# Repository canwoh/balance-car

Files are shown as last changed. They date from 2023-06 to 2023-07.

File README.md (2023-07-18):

# balance-car
## 错误报刊🚫

### 1. PCB设计

#### 滑动开关
开关失效。原理图绘画的时候，把滑动开关其中两个脚都接到了VBAT上，铺铜的时候两脚都接入VBAT，导致开关即使左拨还是右拨中间引脚都会上电。

解决方案：给电源盒焊个开关，将电源盒引出的线接到开关上，再接入PCB中。

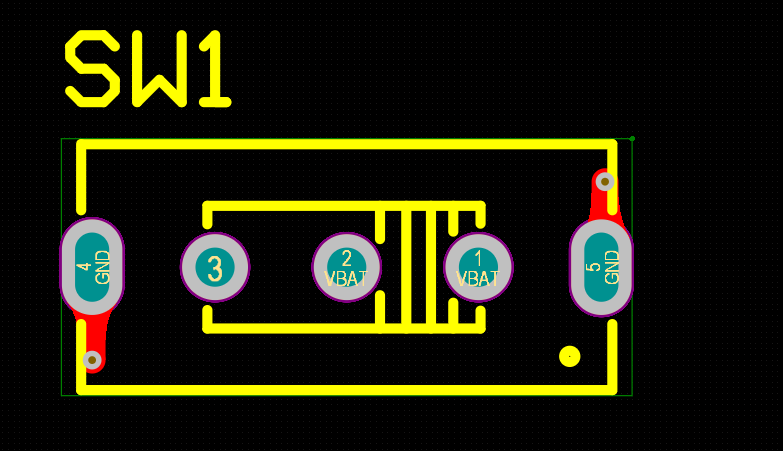
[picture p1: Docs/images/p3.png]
switch


#### OLED模块：
GND与VCC刚好相反，导入PCB封装与实际不符。

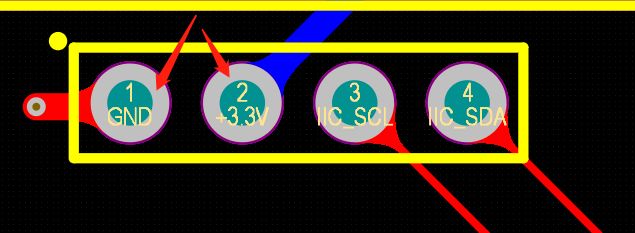
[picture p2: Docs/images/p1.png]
PCB中OLED


#### 电机模块：
注意同一轮子放在左右两侧，DRV8833 相同OUX输出出现两轮转向不一致的情况。

解决方案：右轮BO1与BO2在焊接时，反焊，左轮AO1->AO1 AO2->AO2  右轮BO1->BO2 BO2->BO1

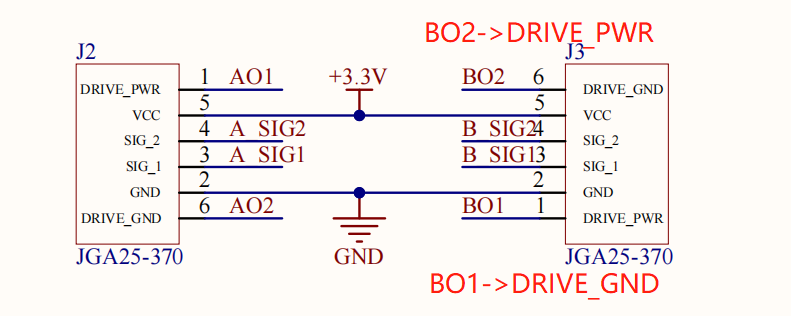
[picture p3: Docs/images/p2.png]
Motor


### 2.CubeMX初始化代码
#### Motors初始化
给电机少配置了两个TIM-PWM输出。PCB设计时给电机配置了两个GPIO，与两个TIM-PWM，实际需要4个PWM输出。

解决方案：后续软件上配置两个PWM Channel，利用中断控制GPIO电平，普通GPIO模拟PWM输出。

### 3.软件编写
#### 软件模拟IIC
* 时序控制错误，移植代码后没有调节时序延迟。查看SSD1306硬件手册时序在400KB/s模式下保底需要2.5us延迟。

* 软件模拟IIC，注意FreeRTOS任务切换时引起的时序问题。

#### FreeRTOS Task Stack Overflow问题
* 任务栈分配不足时，引发一些奇怪的现象。

#### 

## 项目改进🧐
* 项目采用MCU为STM32F103C8T6，Flash空间太小了，只有64KB。采用HAL+FreeRTOS+C/C++混合编写的组合还是太吃力了。编写代码大小受到较大限制。可尝试更换性能更好的MCU。

* 电源模块可以单独拎出来设计，贴片更加方便，压缩水平空间，降低体积。

* 有线器件，可以选择XH接插件方式进行连接。

* 额外设计一个USB串口兼下载模块，版上集成CMSIS-DAP模块(参考项目：vllink_lite)

* 项目中为了学习DMA，蓝牙模块采用UART+DMA模式，推荐采用中断UART接收形式。DMA接收定长输入的效果会更好一些，由于我所使用的上位机发送的信息是不定长且较短，不太好接收。当然DMA接收不定长输入也行，配合中断即可。

## 硬件参考

* 显示屏:OLED 0.96
* 惯性测量单元:MPU6050
* 电机驱动芯片:DRV8833
* 超声波:HC-SR04
* 蓝牙:HC-05
* 电机：淘宝随便买的

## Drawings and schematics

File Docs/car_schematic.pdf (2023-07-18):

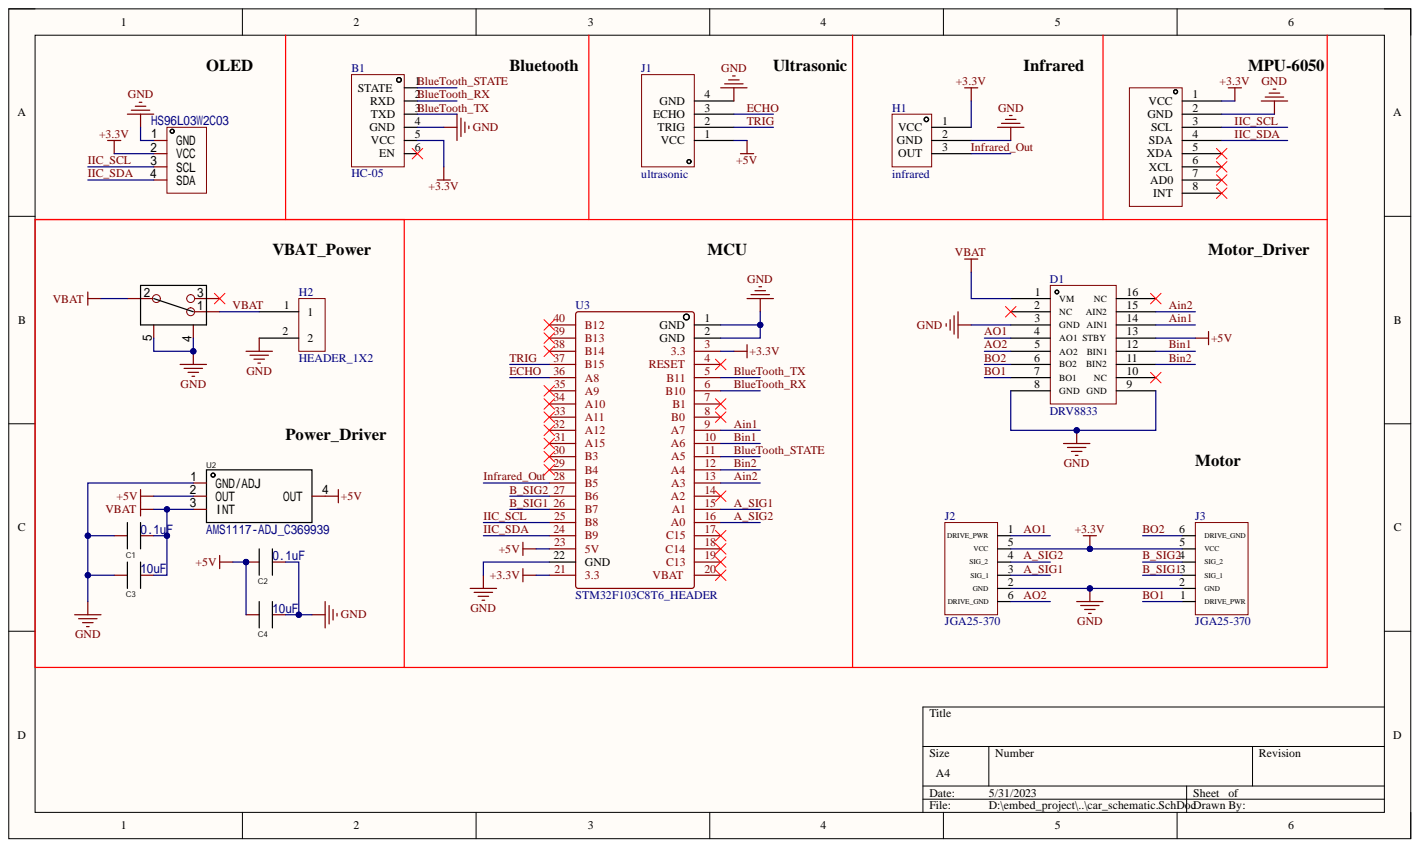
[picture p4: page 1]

Size A4 | Number | Revision

Date: 5/31/2023 | Sheet of
File: D:\embed_project\..\car_schematic.SchDocDrawn By:

Comment | Description | Designator | Footprint | LibRef | Quantity
HC-05 | 蓝牙模块 VCC接3.3 | B1 | HC-05_HEADER | HC-05 | 1
0.1uF | | C1, C2 | C0603 | C0603 | 2
10uF | | C3, C4 | C0603 | C0603 | 2
DRV8833 | 电机驱动 | D1 | DRV8833_HEADER | DRV8833 | 1
infrared | 红外循迹模块 | H1 | RISYM-001_HEADER | RISYM-001 | 1
HEADER_1X2 | | H2 | HEADER_1X2 | HEADER_1X2 | 1
ultrasonic | 超声波模块 Pin Header | J1 | HC-SR04_HEADER | HC-SR04 | 1
JGA25-370 | JGA25-370 直流减速 电机 | J2, J3 | JGA25-370_HEADER | JGA25-370 | 2
SS-12F44-G5_C136718 | 滑动开关G5 | SW1 | SW-TH_SS-12F44-GX | SS-12F44-G5_C136718 | 1
MPU-6050 | Pin Header | U1 | MPU-6050_HEADER | MPU-6050 | 1
AMS1117-ADJ_C369939 | 电源稳压芯片 | U2 | SOT-223_L6.5-W3.5-P2.30-LS7.0-BR | AMS1117-ADJ_C369939 | 1
STM32F103C8T6_HE ADER | Pin Header | U3 | STM32F103C8T6_HE ADER | STM32F103C8T6_HE ADER | 1
HS96L03W2C03 | I2C OLED 0.96 | U4 | OLED-TH_L27.8-W27.2-P2.54_C9900033791 | HS96L03W2C03 | 1

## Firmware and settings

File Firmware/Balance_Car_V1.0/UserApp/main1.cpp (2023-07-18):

#include "common_inc.h"
#include "mpu6050.h"

#define OLED_ADDRESS 0x78
//------------------------c header file scope----------------------------------------
#ifdef __cplusplus
extern "C"
{
#endif
#include "inv_mpu.h"
#include "OLED_Driver.h"
#include <cstring>
#include "bluetooth.h"
#include"control.h"
#ifdef __cplusplus
}
#endif
//----------------------------------------------------------------

// SSD1306 screen(OLED_ADDRESS);
IMU_MPU6050 imu_6050;
//----------------------FreeRtos-----------
extern osMessageQueueId_t uart_rx_dma_queue_id;
extern osThreadId_t defaultTaskHandle;
extern osThreadId_t IMUHandle;
extern osThreadId_t ultrasonicHandle;
//----------------------debug code------
extern char debug_data[8];
uint8_t complete_record;

uint8_t motor_run = 0;
// extern osThreadId_t defaultTaskHandle;
// extern osThreadId_t IMUHandle;
// extern osThreadId_t ultrasonicHandle;
// extern uint32_t time_record[4];
//-----------------User data------------
extern float dist;
extern uint8_t uart_rx_dma_buffer[BUFFER_SIZE];

int balance_pwm,velocity_pwm;
int encoder_left, encoder_right;
int motor1_pwm,motor2_pwm;
//---------------firmware code----------
extern DMA_HandleTypeDef hdma_usart3_rx;
extern UART_HandleTypeDef huart3;
extern TIM_HandleTypeDef htim3;
/*------------------------------------------C++ scope------------------------------------*/
void Motion_Controller_Thread(void *args)
{
    Motor_Init();
    // HAL_GPIO_WritePin(GPIOA,GPIO_PIN_3,GPIO_PIN_RESET);
    // HAL_GPIO_WritePin(GPIOA,GPIO_PIN_4,GPIO_PIN_RESET);
    // __HAL_TIM_SET_COMPARE(&htim3,TIM_CHANNEL_1,MOTOR_DEAD_ZONE);
    // __HAL_TIM_SET_COMPARE(&htim3,TIM_CHANNEL_2,MOTOR_DEAD_ZONE);
    for(;;)
    {
        //读编码器
        encoder_left = Read_Encoder(1);
        encoder_right = -Read_Encoder(2); 
        //直立环
        balance_pwm = Vertical_Ring_PD(imu_6050.imu_data_t.pitch,
                                       imu_6050.imu_data_t.gyro_y);
        //速度环
        velocity_pwm = Velocity_Ring_PI(encoder_left, encoder_right,imu_6050.imu_data_t.pitch);
        motor1_pwm = balance_pwm+velocity_pwm;
        motor2_pwm = balance_pwm+velocity_pwm;
        Motor_Limit(&motor1_pwm,&motor2_pwm);
        if(Turn_OFF(imu_6050.imu_data_t.pitch)){
            __HAL_TIM_SET_COMPARE(&htim3,TIM_CHANNEL_1,0);
            __HAL_TIM_SET_COMPARE(&htim3,TIM_CHANNEL_2,0);
            __HAL_TIM_SET_COMPARE(&htim3,TIM_CHANNEL_3,0);  
            __HAL_TIM_SET_COMPARE(&htim3,TIM_CHANNEL_4,0);  
        }else {
            Set_PWM(motor1_pwm,motor2_pwm);
        }
        osDelay(10);
    }
}

void UART_Recv_DMA_Thread(void *args)
{
    
    HAL_UART_Receive_DMA(&huart3, uart_rx_dma_buffer, BUFFER_SIZE);
    complete_record = 2;
    void *d;
    for (;;)
    {
        osMessageQueueGet(uart_rx_dma_queue_id, &d, NULL, osWaitForever);
        complete_record = 1;
        usart_tx_check();
        (void)d;
    }
}
// ultrasonic measuring distance  25Hz task
void Measure_Distance(void *args)
{
    HAL_GPIO_WritePin(Echo_GPIO_Port, Echo_Pin, GPIO_PIN_RESET);
    for (;;)
    {
        HAL_GPIO_WritePin(Trig_GPIO_Port, Trig_Pin, GPIO_PIN_SET);
        mDelay_us(15);
        HAL_GPIO_WritePin(Trig_GPIO_Port, Trig_Pin, GPIO_PIN_RESET);
        osDelay(40);
    }
}

// imu task handle function 200Hz task
void IMU_Get_Data(void *args)
{
    vTaskSuspendAll();
    while (mpu_dmp_init())
    {
    }

    OLED_Init();
    xTaskResumeAll();
    for (;;)
    {
        vTaskSuspendAll();
        mpu_dmp_get_data(&imu_6050.imu_data_t);

        xTaskResumeAll();
        osDelay(5);
    }
}
// initialize and show data 5Hz task
// void Main(void *args)
// {
//     OLED_Init();
//     Motor_Init();
//     HAL_GPIO_WritePin(GPIOA,GPIO_PIN_3,GPIO_PIN_RESET);
//     HAL_GPIO_WritePin(GPIOA,GPIO_PIN_4,GPIO_PIN_RESET);
//     __HAL_TIM_SET_COMPARE(&htim3,TIM_CHANNEL_1,MOTOR_DEAD_ZONE);
//     __HAL_TIM_SET_COMPARE(&htim3,TIM_CHANNEL_2,MOTOR_DEAD_ZONE);
//     //char *msg = (char *)pvPortMalloc(16);
//     for (;;)
//     {
//         vTaskSuspendAll();
//         // OLED_ShowString(1,1,"mem:")
//         // memset(msg, 0, 16);
//         // sprintf(msg, "pitch:%.5f", imu_6050.imu_data_t.pitch);
//         // OLED_ShowString(1, 1, msg);
//         // // printf("%s\r\n",msg);
//         // memset(msg, 0, 16);
//         // sprintf(msg, "roll:%.5f", imu_6050.imu_data_t.roll);
//         // OLED_ShowString(2, 1, msg);
//         // // printf("%s\r\n",msg);
//         // memset(msg, 0, 16);
//         // sprintf(msg, "yaw:%.5f", imu_6050.imu_data_t.yaw);
//         // OLED_ShowString(3,1,msg);


//         OLED_ShowNum(4,1,motor_run,4);
      
//         xTaskResumeAll();
//         osDelay(200);
//     }
//     // vPortFree(msg);
// }

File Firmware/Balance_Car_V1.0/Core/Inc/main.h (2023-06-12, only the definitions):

#define AIN2_Pin GPIO_PIN_3
#define AIN2_GPIO_Port GPIOA
#define BIN2_Pin GPIO_PIN_4
#define BIN2_GPIO_Port GPIOA
#define Bluetooth_State_Pin GPIO_PIN_5
#define Bluetooth_State_GPIO_Port GPIOA
#define Trig_Pin GPIO_PIN_15
#define Trig_GPIO_Port GPIOB
#define Echo_Pin GPIO_PIN_8
#define Echo_GPIO_Port GPIOA
#define Echo_EXTI_IRQn EXTI9_5_IRQn
#define infrared_Pin GPIO_PIN_5
#define infrared_GPIO_Port GPIOB
#define I2C_SCL_Pin GPIO_PIN_8
#define I2C_SCL_GPIO_Port GPIOB
#define I2C_SDA_Pin GPIO_PIN_9
#define I2C_SDA_GPIO_Port GPIOB

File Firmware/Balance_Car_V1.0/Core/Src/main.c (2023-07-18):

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
/* Includes ------------------------------------------------------------------*/
#include "main.h"
#include "cmsis_os.h"
#include "dma.h"
#include "tim.h"
#include "usart.h"
#include "gpio.h"

/* USER CODE BEGIN Includes */
#include"OLED_Driver.h"
extern uint8_t complete_record;
extern osMessageQueueId_t uart_rx_dma_queue_id;
extern uint32_t time_record[4];
extern float dist;

/* USER CODE END Includes */


void SystemClock_Config(void);
void MX_FREERTOS_Init(void);
/**
  * @brief  The application entry point.
  * @retval int
  */
int main(void)
{
  /* MCU Configuration--------------------------------------------------------*/

  /* Reset of all peripherals, Initializes the Flash interface and the Systick. */
  HAL_Init();

  /* Configure the system clock */
  SystemClock_Config();

  /* Initialize all configured peripherals */
  MX_GPIO_Init();
  MX_DMA_Init();
  MX_USART3_UART_Init();
  MX_TIM2_Init();
  MX_TIM3_Init();
  MX_TIM4_Init();
  /* Init scheduler */
  osKernelInitialize();  /* Call init function for freertos objects (in freertos.c) */
  MX_FREERTOS_Init();

  /* Start scheduler */
  osKernelStart();
  /* We should never get here as control is now taken by the scheduler */
  /* Infinite loop */
  /* USER CODE BEGIN WHILE */
  while (1)
  {
    /* USER CODE END WHILE */
    
    /* USER CODE BEGIN 3 */
  }
  /* USER CODE END 3 */
}

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
/* USER CODE BEGIN 4 */

/**
  * @brief  PWM Pulse finished callback in non-blocking mode
  * @param  htim TIM handle
  * @retval None
  */
void HAL_TIM_PWM_PulseFinishedCallback(TIM_HandleTypeDef *htim)
{
    // if(htim->Instance == TIM3)
    // {
    //   if(htim->Channel == HAL_TIM_ACTIVE_CHANNEL_3)
    //   {
    //      HAL_GPIO_WritePin(GPIOA,GPIO_PIN_3,RESET);
    //   }
    //   if(htim->Channel == HAL_TIM_ACTIVE_CHANNEL_4)
    //   {
    //     HAL_GPIO_WritePin(GPIOA,GPIO_PIN_4,RESET);
    //   }
    // }
    if(htim->Channel == HAL_TIM_ACTIVE_CHANNEL_3)
    {
        GPIOA->BRR = GPIO_PIN_3;
    } else if(htim->Channel == HAL_TIM_ACTIVE_CHANNEL_4)
    {
        GPIOA->BRR = GPIO_PIN_4;
    }
}



/*
  *@brief UART Callback function
*/
void HAL_UART_RxCpltCallback(UART_HandleTypeDef *huart)
{
  if(USART3 == huart->Instance){
      void *d = (void*)1;
      __HAL_UART_CLEAR_IDLEFLAG(huart);
      osMessageQueuePut(uart_rx_dma_queue_id,&d,0,0);
  }
  //osMessageQueuePut(uart_rx_dma_queue_id,&d,0,0); 
}

/*
  * @brief  Echo Callback
  * @param  GPIO_Pin ：Echo_Pin
  * @retval 无
*/
void HAL_GPIO_EXTI_Callback(uint16_t GPIO_Pin)
{
  __HAL_GPIO_EXTI_CLEAR_IT(GPIO_Pin);
  if(GPIO_Pin == Echo_Pin)
  {
    //pull up trigger
    if(HAL_GPIO_ReadPin(Echo_GPIO_Port,Echo_Pin)==GPIO_PIN_SET)
    {
        time_record[1] = get_sysTick_ms();
        time_record[3] = get_sysTick_us_part();

    }
    //pull down trigger
    else if(HAL_GPIO_ReadPin(Echo_GPIO_Port,Echo_Pin)==GPIO_PIN_RESET)
    {
      //us 
        uint32_t total_time;
        time_record[0] = get_sysTick_ms();
        time_record[2] = get_sysTick_us_part();
        total_time = (time_record[0] - time_record[1])*1000 + time_record[3] - time_record[2]; 
        dist = (float)total_time * 0.17;
    }
  }
}

/* USER CODE END 4 */

/**
  * @brief  Period elapsed callback in non blocking mode
  * @note   This function is called  when TIM1 interrupt took place, inside
  * HAL_TIM_IRQHandler(). It makes a direct call to HAL_IncTick() to increment
  * a global variable "uwTick" used as application time base.
  * @param  htim : TIM handle
  * @retval None
  */
void HAL_TIM_PeriodElapsedCallback(TIM_HandleTypeDef *htim)
{
  /* USER CODE BEGIN Callback 0 */
   if(TIM3->CCR3 != 0)
        GPIOA->BSRR = GPIO_PIN_3;
    if(TIM3->CCR4 != 0)
        GPIOA->BSRR = GPIO_PIN_4;
  /* USER CODE END Callback 0 */
  if (htim->Instance == TIM1) {
    HAL_IncTick();
  }
  /* USER CODE BEGIN Callback 1 */
  // if (htim->Instance == TIM3)
  // {
  //    if((__HAL_TIM_GET_COMPARE(htim,TIM_CHANNEL_3))!=0)
  //     {
  //        HAL_GPIO_WritePin(GPIOA,GPIO_PIN_3,SET);
  //     }
  //     if((__HAL_TIM_GET_COMPARE(htim,TIM_CHANNEL_4))!=0)
  //     {
  //       HAL_GPIO_WritePin(GPIOA,GPIO_PIN_4,SET);
  //     }
  // }
  /* USER CODE END Callback 1 */
}

/**
  * @brief  This function is executed in case of error occurrence.
  * @retval None
  */
void Error_Handler(void)
{
  /* USER CODE BEGIN Error_Handler_Debug */
  /* User can add his own implementation to report the HAL error return state */
  __disable_irq();
  while (1)
  {
  }
  /* USER CODE END Error_Handler_Debug */
}

#ifdef  USE_FULL_ASSERT
/**
  * @brief  Reports the name of the source file and the source line number
  *         where the assert_param error has occurred.
  * @param  file: pointer to the source file name
  * @param  line: assert_param error line source number
  * @retval None
  */
void assert_failed(uint8_t *file, uint32_t line)
{
  /* USER CODE BEGIN 6 */
  /* User can add his own implementation to report the file name and line number,
     ex: printf("Wrong parameters value: file %s on line %d\r\n", file, line) */
  /* USER CODE END 6 */
}
#endif /* USE_FULL_ASSERT */

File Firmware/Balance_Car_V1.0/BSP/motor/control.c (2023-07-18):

#include "control.h"



extern TIM_HandleTypeDef htim2;
extern TIM_HandleTypeDef htim3;
extern TIM_HandleTypeDef htim4;


Motor_PID_ARGS PID_ARGS = {
    .Balance_Kp = -240, //raw value:400 Processed value : -240
    .Balance_Ki = 0,//UNUSED
    .Balance_Kd = -0.68,  //raw value:1.1 Processed value : -0.67
    .Velocity_Kp = -135,
    .Velocity_Ki = -0.67,
    .Velocity_Kd = 0,//UNUSED
    .Turn_Kp = 0,//UNUSED
    .Turn_Ki = 0,//UNUSED
    .Turn_Kd = 0,//UNUSED
};

// 读取编码器值
//@param Motorx(1 or 2) : 1)：编码器1 TIM2  2)：编码器2 TIM4
int Read_Encoder(uint8_t Motorx)
{
    int Encoder_Value;
    switch (Motorx)
    {
    case 1:
        Encoder_Value = (short)TIM2->CNT;
        TIM2->CNT = 0;
        break;
    case 2:
        Encoder_Value = (short)TIM4->CNT;
        TIM4->CNT = 0;
        break;
    default:
        Encoder_Value = 0;
    }
    return Encoder_Value;
}

/***************************************
 *@name：直立PD控制
 *@param：角度、机械平衡角度（机械中值）、角速度
 *@return：直立控制PWM
 *
 */
int Vertical_Ring_PD(float pitch, float Gypo)
{
    float Bias;  // 角度误差
    int balance; // 直立环计算出来的电机控制pwm
    Bias = pitch - MECHANICAL_MEDIAN_ANGLE;
    balance = PID_ARGS.Balance_Kp * Bias + PID_ARGS.Balance_Kd * Gypo;
    return balance;
}


int Velocity_Ring_PI(int Encoder_Left, int Encoder_Right,float pitch)
{
    float Velocity, Encoder_Least;
    static float Encoder, Encoder_Integral;
    // static float Movement;
    //===获取最新速度偏差==测量速度（左右编码器之和）-目标速度（此处为零）
    Encoder_Least = (Encoder_Left + Encoder_Right) - 0;
    Encoder *= 0.8; // 一阶低通滤波
    Encoder += Encoder_Least * 0.2;
    Encoder_Integral += Encoder;
    // 积分限幅
    if (Encoder_Integral > 10000)
        Encoder_Integral = 10000;
    if (Encoder_Integral < -10000)
        Encoder_Integral = -10000;
    // 速度控制

    Velocity = PID_ARGS.Velocity_Kp * Encoder + PID_ARGS.Velocity_Ki * Encoder_Integral;
    if(pitch<-68||pitch>68)Encoder_Integral=0;
    return Velocity;
}

void Motor_Limit(int *PWM1, int *PWM2)
{
    int m_pwm1 = *PWM1;
    int m_pwm2 = *PWM2;
    if (m_pwm1 > 0)
    {
        *PWM1 = m_pwm1 > 3034 ? 3034 : m_pwm1;
    }
    else
    {
        *PWM1 = m_pwm1 < -3034 ? -3034 : m_pwm1;
    }
    if (m_pwm2 > 0)
    {
        *PWM2 = m_pwm2 > 3034 ? 3034 : m_pwm2;
    }
    else
    {
        *PWM2 = m_pwm2 < -3034 ? -3034 : m_pwm2;
    }
}


int ABS(int a)
{
	a = a > 0 ? a : (-a);
	return a;
}

uint8_t Turn_OFF(float pitch)
{
    if(pitch<-68||pitch>68)
    {
        return 1;
    }
    return 0;
}

void Set_PWM(int motor1,int motor2)
{
    if(motor1>0)
    {
        __HAL_TIM_SET_COMPARE(&htim3,TIM_CHANNEL_1,0);
        __HAL_TIM_SET_COMPARE(&htim3,TIM_CHANNEL_3,MOTOR_DEAD_ZONE+ABS(motor1)*1.17);  
    }else
    {
        __HAL_TIM_SET_COMPARE(&htim3,TIM_CHANNEL_1,MOTOR_DEAD_ZONE+ABS(motor1)*1.17);
        __HAL_TIM_SET_COMPARE(&htim3,TIM_CHANNEL_3,0);
    }
    if(motor2>0)
    {
        __HAL_TIM_SET_COMPARE(&htim3,TIM_CHANNEL_2,0);
        __HAL_TIM_SET_COMPARE(&htim3,TIM_CHANNEL_4,MOTOR_DEAD_ZONE+ABS(motor1)*1.17);  
    }
    else
    {
        __HAL_TIM_SET_COMPARE(&htim3,TIM_CHANNEL_2,MOTOR_DEAD_ZONE+ABS(motor1)*1.17);
        __HAL_TIM_SET_COMPARE(&htim3,TIM_CHANNEL_4,0);
    }

}

void Motor_Init(void)
{

    __HAL_TIM_ENABLE_IT(&htim3,TIM_IT_UPDATE);
    HAL_TIM_Encoder_Start(&htim2, TIM_CHANNEL_ALL);
    HAL_TIM_Encoder_Start(&htim4, TIM_CHANNEL_ALL);
    HAL_TIM_PWM_Start(&htim3,TIM_CHANNEL_1);
    HAL_TIM_PWM_Start(&htim3,TIM_CHANNEL_2);
    HAL_TIM_PWM_Start_IT(&htim3,TIM_CHANNEL_3);
    HAL_TIM_PWM_Start_IT(&htim3,TIM_CHANNEL_4);
    HAL_GPIO_WritePin(GPIOA,GPIO_PIN_3,GPIO_PIN_RESET);
    HAL_GPIO_WritePin(GPIOA,GPIO_PIN_4,GPIO_PIN_RESET);
}

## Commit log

2023-05-28 Add:upload Hardware PCB file
    [Car_PCB.PrjPcb, car_PCB.PcbDoc, car_PcbLib.PcbLib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]
2023-06-08 Add : Configure the Device Init,Fix:Makefile Bug
    [main.c, main.h, main1.cpp]
2023-06-09 Add : 1)none-test module SSD1306 2)redirect printf,use uart3 to debug for a short time
    [main.c, main.h, main1.cpp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]
2023-06-12 Add : Safe print,Ultrasonic(uncomplete)
2023-07-05 ultrasonic,imu,oled modules have been finished
2023-07-18 add : motors control

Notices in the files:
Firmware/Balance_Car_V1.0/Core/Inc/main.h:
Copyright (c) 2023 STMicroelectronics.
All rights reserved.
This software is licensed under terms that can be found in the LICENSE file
